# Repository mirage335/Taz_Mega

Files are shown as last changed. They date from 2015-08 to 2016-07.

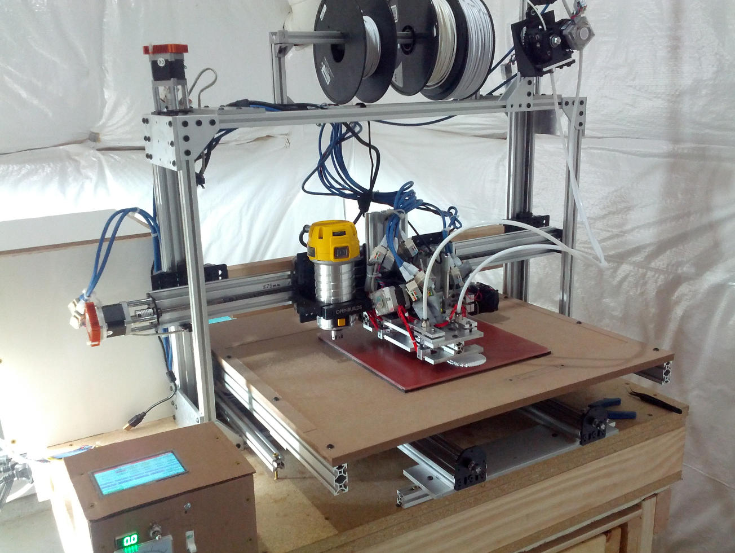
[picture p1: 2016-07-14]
Photos/EarlyPrint.jpg

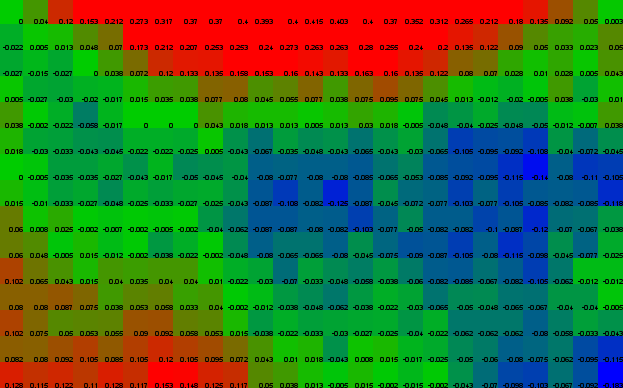
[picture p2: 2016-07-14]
Photos/InitialTopography.jpg

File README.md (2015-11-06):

Copyright (C) 2015 mirage335
See the end of the file for license conditions.
See license.txt for Taz_Mega license conditions.

mirage335.member.hacdc.org

Large-scale advanced multi-tool desktop factory derived from LulzBot Taz. Successor to FlexReplicator.

Intended to simultaneously operate multiple at least milling, laser, extrusion (FDM 3D Printing), and inkjet (powder 3D printing, 2D coloring) tools.

Total cost is estimated at $1,574.45. Normal Taz bulk production costs using this setup would be closer to $1k/unit, probable savings as follows.

Custom Plates - $200/unit.
Y-axis deduplication - $200/unit.
X/Y axis length reduction - $150/unit

#Tweaks
Z-Axis motor mounting plate edges protrude into the frame extrusions, and must be ground slightly to compensate.

Spacer blocks may not leave adequate clearance for the most ideal gantry plate screw locations. Solvable with moderate grinding.

Lock nuts used in wheel assemblies may conflict with some metal plates. Moderate grinding, or use of jam nuts with threadlocker, are solutions.

Y-Axis threaded rod may not be matched to adequately tight tolerances (<<0.3%). Tightly spring-loading all couplings to one of the two threaded rods may alleviate binding at minimal loss of performance. For light-duty work, only one threaded rod is actually necessary.

Do not overtighten joints between gantry plates and aluminum extrusions, as this can significantly overload of the wheel assemblies.

Many more metric screws and Tee Nuts may be required. In particular, some low-profile M5x12mm screws are required to join the Y-axis assembly to the frame. These can be made by grinding down M5x15mm screws from Open Builds.

Right angle brackets from Open Builds may not be suitable for joining the Z-axis extrusions to the frame. Corner cubes are more than adequate.

#Electronics
Duet electronics with PatchRap panel STRONGLY recommended. Heatsinkng the motor drivers would also be wise, as maximum rated current should be used.

#Copyright Extensions
Files embedded into the design by mirage335 with a less restrictive license than GPLv3 place any derrived works under that license. This is definied to include any files pulled into the repository by mirage335 .

#Copyright
This file is part of Taz_Mega.

Taz_Mega is free software: you can redistribute it and/or modify
it under the terms of the GNU General Public License as published by
the Free Software Foundation, either version 3 of the License, or
(at your option) any later version.

Taz_Mega is distributed in the hope that it will be useful,
but WITHOUT ANY WARRANTY; without even the implied warranty of
MERCHANTABILITY or FITNESS FOR A PARTICULAR PURPOSE.  See the
GNU General Public License for more details.

You should have received a copy of the GNU General Public License
along with Taz_Mega.  If not, see <http://www.gnu.org/licenses/>.

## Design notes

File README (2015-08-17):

Copyright (C) 2013 mirage335
See the end of the file for license conditions.
See license.txt for Taz_Mega license conditions.

mirage335.member.hacdc.org

Large-scale advanced multi-tool desktop factory derived from LulzBot Taz. Successor to FlexReplicator.

Intended to simultaneously operate multiple milling, laser, extrusion (FDM 3D Printing), and inkjet (powder 3D printing, 2D coloring) tools.

SolidWorks files will eventually be replaced with FreeCAD, pending initial construction. See render.png for assembly overview, or download free eDrawings viewer for further investigation.

_Copyright Extensions_
Files embedded into the design by mirage335 with a less restrictive license than GPLv3 place any derrived works under that license. This is definied to include any files pulled into the repository by mirage335 .

_Copyright_
This file is part of Taz_Mega.

Taz_Mega is free software: you can redistribute it and/or modify
it under the terms of the GNU General Public License as published by
the Free Software Foundation, either version 3 of the License, or
(at your option) any later version.

Taz_Mega is distributed in the hope that it will be useful,
but WITHOUT ANY WARRANTY; without even the implied warranty of
MERCHANTABILITY or FITNESS FOR A PARTICULAR PURPOSE.  See the
GNU General Public License for more details.

You should have received a copy of the GNU General Public License
along with Taz_Mega.  If not, see <http://www.gnu.org/licenses/>.

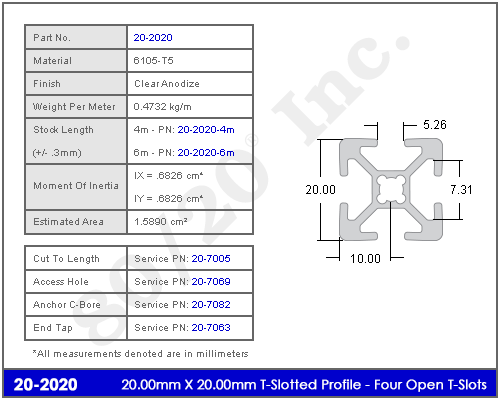
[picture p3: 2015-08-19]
_hardware/Extrusions/_ref/8020profile.gif

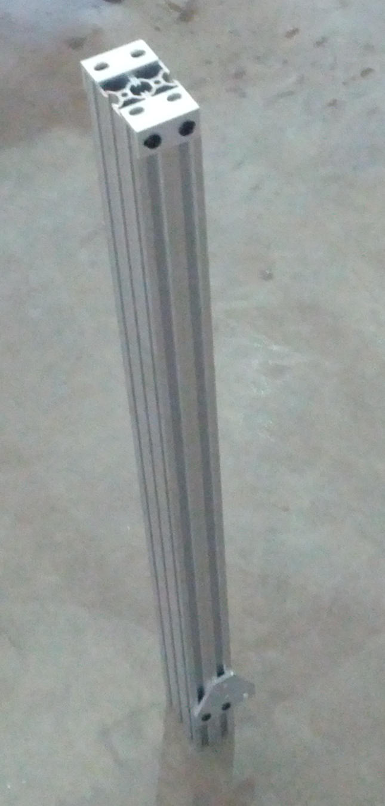
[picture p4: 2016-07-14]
Photos/EqualLength.jpg

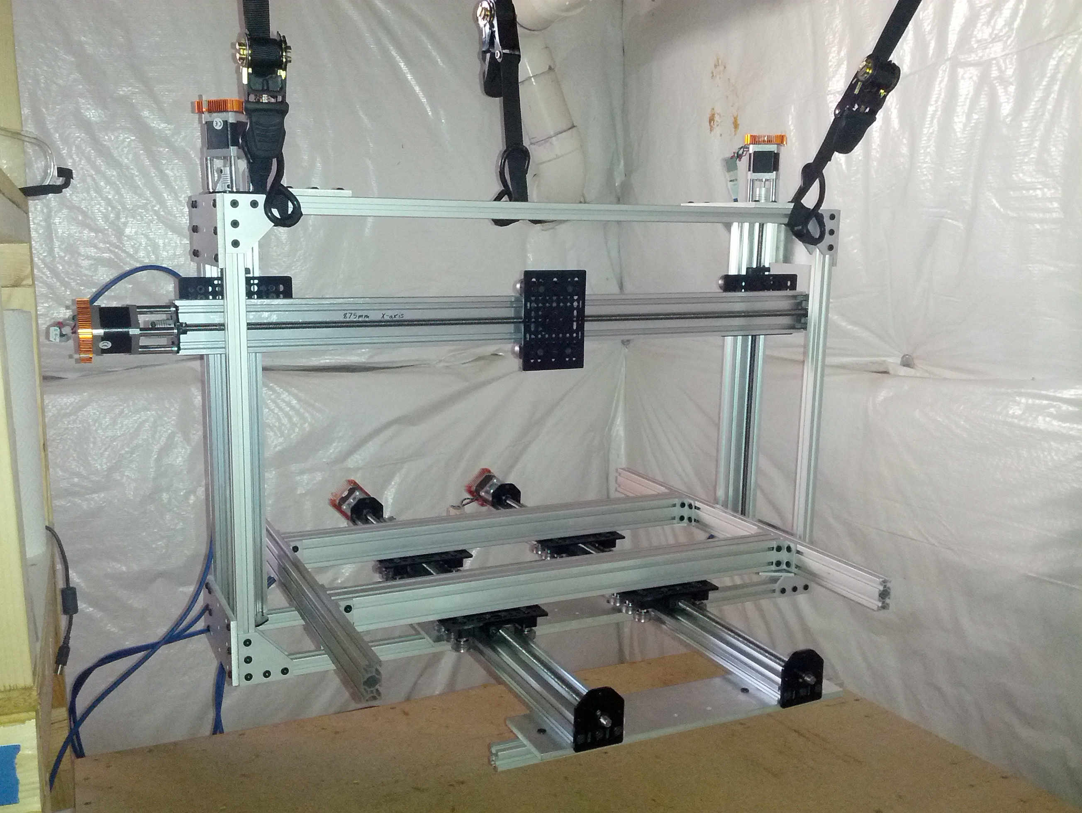
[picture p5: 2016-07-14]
Photos/Suspended.jpg

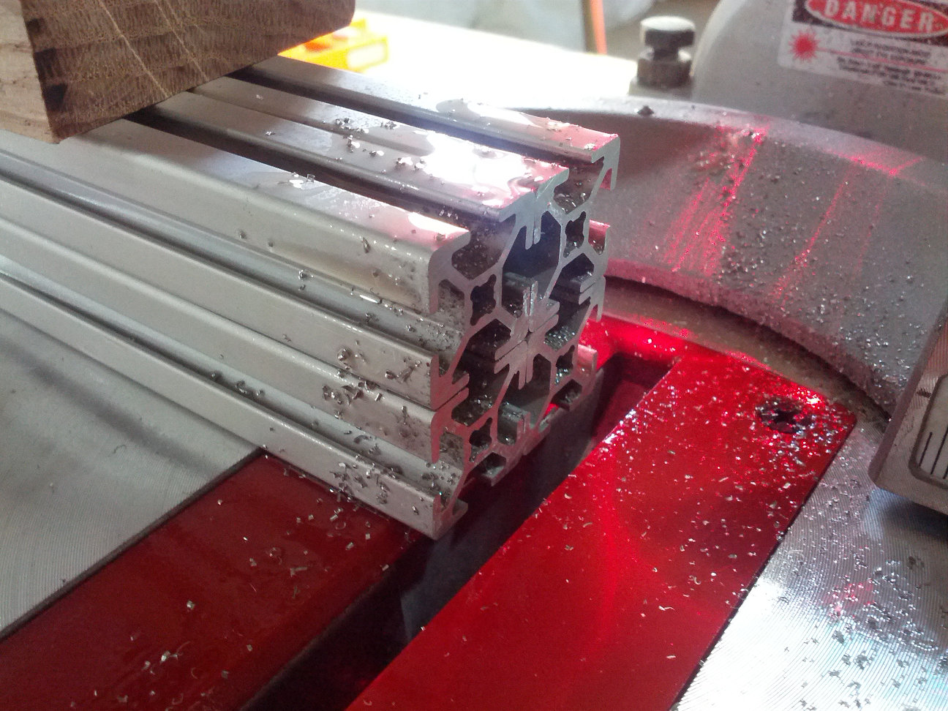
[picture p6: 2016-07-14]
Photos/Cutting.jpg

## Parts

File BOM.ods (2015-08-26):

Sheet: Total_OpenBuilds_DeDup
Description | Qualifiers | Qty | Multiplier | Total | Cost | Total | Supplier
ACME Anti-Backlash Nut Block |  |  |  | 7 | $9.85 | $68.95 | http://openbuildspartstore.com/anti-backlash-nut-block-for-8mm-metric-acme-lead-screw/
ACME LeadScrew |  |  |  | 5 | $31.50 | $157.50 | http://openbuildspartstore.com/8mm-metric-acme-lead-screw/
Cube Corner Connector |  |  |  | 8 | $3.25 | $26.00 | http://openbuildspartstore.com/cube-corner-connector/
Eccentric Spacer, 6mm |  |  |  | 21 | $2.00 | $42.00 | http://openbuildspartstore.com/eccentric-spacer/
Flexible Coupling |  |  |  | 5 | $6.35 | $31.75 | http://openbuildspartstore.com/5mm-8mm-flexible-coupling/
Gantry Plates, Universal V-Slot |  |  |  | 7 | $12.00 | $84.00 | http://openbuildspartstore.com/v-slot-gantry-plates/
Joining Plate, 90deg |  |  |  | 8 | $4.80 | $38.40 | http://openbuildspartstore.com/90-degree-joining-plate/
Joining Plate, T |  |  |  | 4 | $4.65 | $18.60 | http://openbuildspartstore.com/t-joining-plate/
L Bracket | Double |  |  | 6 | $1.50 | $9.00 | http://openbuildspartstore.com/l-bracket/
L Bracket | Tripple |  |  | 6 | $1.50 | $9.00 | http://openbuildspartstore.com/l-bracket/
Lock Collar |  |  |  | 15 | $0.90 | $13.50 | http://openbuildspartstore.com/lock-collar/
Low Profile M5 35mm Screws |  |  |  | 42 | $0.20 | $8.40 | http://openbuildspartstore.com/low-profile-screws-m5/
M3 45mm Screw |  |  |  | 15 | $0.25 | $3.75 | http://openbuildspartstore.com/m3-cap-head-screws/
Screw-M5x10 |  |  |  | 130 | $0.13 | $16.38 | http://openbuildspartstore.com/low-profile-screws-m5/
Screw-M5x8 |  |  |  | 130 | $0.13 | $16.38 | http://openbuildspartstore.com/low-profile-screws-m5/
Set Screw |  |  |  | 15 | $0.07 | $1.05 | http://openbuildspartstore.com/set-screw/
Spacer Blocks |  |  |  | 14 | $3.95 | $55.30 | http://openbuildspartstore.com/spacer-block/
Spacer, 35mm Aluminum |  |  |  | 15 | $0.70 | $10.50 | http://openbuildspartstore.com/aluminum-spacers/
Spacer, 6mm Aluminum |  |  |  | 42 | $0.30 | $12.60 | http://openbuildspartstore.com/aluminum-spacers/
TeeNut-M5x10 |  |  |  | 130 | $0.20 | $25.74 | http://openbuildspartstore.com/tee-nuts-25-pack/
Threaded Rod Motor Mount Plates, NEMA17 |  |  |  | 10 | $6.95 | $69.50 | http://openbuildspartstore.com/threaded-rod-plate-for-nema-17-stepper-motor/
Thruster Bearings |  |  |  | 15 | $1.00 | $15.00 | http://openbuildspartstore.com/ball-bearing-688z-8x16x5/
V-Slot Rail |  |  |  | 3 | $15.50 | $46.50 | http://openbuildspartstore.com/v-slot-linear-rail/
V-Slot Rail | 500mm |  |  | 2 | $7.50 | $15.00 | http://openbuildspartstore.com/v-slot-linear-rail/
Wheel Kits |  |  |  | 42 | $6.75 | $283.50 | http://openbuildspartstore.com/xtreme-solid-v-wheel-kit/
 |  |  |  |  |  | $1,078.30
 |  |  |  |  |  | $1,078.30

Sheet: Total_OpenBuilds
Description | Qualifiers | Qty | Multiplier | Total | Cost | Total | Supplier
Flexible Coupling |  | 1 | 1 | 1 | $6.35 | $6.35 | http://openbuildspartstore.com/5mm-8mm-flexible-coupling/
Flexible Coupling |  | 1 | 2 | 2 | $6.35 | $12.70 | http://openbuildspartstore.com/5mm-8mm-flexible-coupling/
Flexible Coupling |  | 1 | 2 | 2 | $6.35 | $12.70 | http://openbuildspartstore.com/5mm-8mm-flexible-coupling/
ACME LeadScrew |  | 1 | 1 | 1 | $31.50 | $31.50 | http://openbuildspartstore.com/8mm-metric-acme-lead-screw/
ACME LeadScrew |  | 1 | 2 | 2 | $31.50 | $63.00 | http://openbuildspartstore.com/8mm-metric-acme-lead-screw/
ACME LeadScrew |  | 1 | 2 | 2 | $31.50 | $63.00 | http://openbuildspartstore.com/8mm-metric-acme-lead-screw/
Joining Plate, 90deg |  | 8 | 1 | 8 | $4.80 | $38.40 | http://openbuildspartstore.com/90-degree-joining-plate/
Spacer, 35mm Aluminum |  | 3 | 1 | 3 | $0.70 | $2.10 | http://openbuildspartstore.com/aluminum-spacers/
Spacer, 6mm Aluminum |  | 6 | 1 | 6 | $0.30 | $1.80 | http://openbuildspartstore.com/aluminum-spacers/
Spacer, 35mm Aluminum |  | 3 | 2 | 6 | $0.70 | $4.20 | http://openbuildspartstore.com/aluminum-spacers/
Spacer, 6mm Aluminum |  | 6 | 4 | 24 | $0.30 | $7.20 | http://openbuildspartstore.com/aluminum-spacers/
Spacer, 35mm Aluminum |  | 3 | 2 | 6 | $0.70 | $4.20 | http://openbuildspartstore.com/aluminum-spacers/
Spacer, 6mm Aluminum |  | 6 | 2 | 12 | $0.30 | $3.60 | http://openbuildspartstore.com/aluminum-spacers/
ACME Anti-Backlash Nut Block |  | 1 | 1 | 1 | $9.85 | $9.85 | http://openbuildspartstore.com/anti-backlash-nut-block-for-8mm-metric-acme-lead-screw/
ACME Anti-Backlash Nut Block |  | 1 | 4 | 4 | $9.85 | $39.40 | http://openbuildspartstore.com/anti-backlash-nut-block-for-8mm-metric-acme-lead-screw/
ACME Anti-Backlash Nut Block |  | 1 | 2 | 2 | $9.85 | $19.70 | http://openbuildspartstore.com/anti-backlash-nut-block-for-8mm-metric-acme-lead-screw/
Thruster Bearings |  | 3 | 1 | 3 | $1.00 | $3.00 | http://openbuildspartstore.com/ball-bearing-688z-8x16x5/
Thruster Bearings |  | 3 | 2 | 6 | $1.00 | $6.00 | http://openbuildspartstore.com/ball-bearing-688z-8x16x5/
Thruster Bearings |  | 3 | 2 | 6 | $1.00 | $6.00 | http://openbuildspartstore.com/ball-bearing-688z-8x16x5/
Cube Corner Connector |  | 8 | 1 | 8 | $3.25 | $26.00 | http://openbuildspartstore.com/cube-corner-connector/
Eccentric Spacer, 6mm |  | 3 | 1 | 3 | $2.00 | $6.00 | http://openbuildspartstore.com/eccentric-spacer/
Eccentric Spacer, 6mm |  | 3 | 4 | 12 | $2.00 | $24.00 | http://openbuildspartstore.com/eccentric-spacer/
Eccentric Spacer, 6mm |  | 3 | 2 | 6 | $2.00 | $12.00 | http://openbuildspartstore.com/eccentric-spacer/
L Bracket | Double | 6 | 1 | 6 | $1.50 | $9.00 | http://openbuildspartstore.com/l-bracket/
L Bracket | Tripple | 6 | 1 | 6 | $1.50 | $9.00 | http://openbuildspartstore.com/l-bracket/
Lock Collar |  | 3 | 1 | 3 | $0.90 | $2.70 | http://openbuildspartstore.com/lock-collar/
Lock Collar |  | 3 | 2 | 6 | $0.90 | $5.40 | http://openbuildspartstore.com/lock-collar/
Lock Collar |  | 3 | 2 | 6 | $0.90 | $5.40 | http://openbuildspartstore.com/lock-collar/
Screw-M5x8 |  | 130 | 1 | 130 | $0.13 | $16.38 | http://openbuildspartstore.com/low-profile-screws-m5/
Screw-M5x10 |  | 130 | 1 | 130 | $0.13 | $16.38 | http://openbuildspartstore.com/low-profile-screws-m5/
Low Profile M5 35mm Screws |  | 6 | 1 | 6 | $0.20 | $1.20 | http://openbuildspartstore.com/low-profile-screws-m5/
Low Profile M5 35mm Screws |  | 6 | 4 | 24 | $0.20 | $4.80 | http://openbuildspartstore.com/low-profile-screws-m5/
Low Profile M5 35mm Screws |  | 6 | 2 | 12 | $0.20 | $2.40 | http://openbuildspartstore.com/low-profile-screws-m5/
M3 45mm Screw |  | 3 | 1 | 3 | $0.25 | $0.75 | http://openbuildspartstore.com/m3-cap-head-screws/
M3 45mm Screw |  | 3 | 2 | 6 | $0.25 | $1.50 | http://openbuildspartstore.com/m3-cap-head-screws/
M3 45mm Screw |  | 3 | 2 | 6 | $0.25 | $1.50 | http://openbuildspartstore.com/m3-cap-head-screws/
Set Screw |  | 3 | 1 | 3 | $0.07 | $0.21 | http://openbuildspartstore.com/set-screw/
Set Screw |  | 3 | 2 | 6 | $0.07 | $0.42 | http://openbuildspartstore.com/set-screw/
Set Screw |  | 3 | 2 | 6 | $0.07 | $0.42 | http://openbuildspartstore.com/set-screw/
Spacer Blocks |  | 2 | 1 | 2 | $3.95 | $7.90 | http://openbuildspartstore.com/spacer-block/
Spacer Blocks |  | 2 | 4 | 8 | $3.95 | $31.60 | http://openbuildspartstore.com/spacer-block/
Spacer Blocks |  | 2 | 2 | 4 | $3.95 | $15.80 | http://openbuildspartstore.com/spacer-block/
Joining Plate, T |  | 4 | 1 | 4 | $4.65 | $18.60 | http://openbuildspartstore.com/t-joining-plate/
TeeNut-M5x10 |  | 130 | 1 | 130 | $0.20 | $25.74 | http://openbuildspartstore.com/tee-nuts-25-pack/
Threaded Rod Motor Mount Plates, NEMA17 |  | 2 | 1 | 2 | $6.95 | $13.90 | http://openbuildspartstore.com/threaded-rod-plate-for-nema-17-stepper-motor/
Threaded Rod Motor Mount Plates, NEMA17 |  | 2 | 2 | 4 | $6.95 | $27.80 | http://openbuildspartstore.com/threaded-rod-plate-for-nema-17-stepper-motor/
Threaded Rod Motor Mount Plates, NEMA17 |  | 2 | 2 | 4 | $6.95 | $27.80 | http://openbuildspartstore.com/threaded-rod-plate-for-nema-17-stepper-motor/
Gantry Plates, Universal V-Slot |  | 1 | 1 | 1 | $12.00 | $12.00 | http://openbuildspartstore.com/v-slot-gantry-plates/
Gantry Plates, Universal V-Slot |  | 1 | 4 | 4 | $12.00 | $48.00 | http://openbuildspartstore.com/v-slot-gantry-plates/
Gantry Plates, Universal V-Slot |  | 1 | 2 | 2 | $12.00 | $24.00 | http://openbuildspartstore.com/v-slot-gantry-plates/
V-Slot Rail |  | 1 | 1 | 1 | $15.50 | $15.50 | http://openbuildspartstore.com/v-slot-linear-rail/
V-Slot Rail |  | 1 | 2 | 2 | $15.50 | $31.00 | http://openbuildspartstore.com/v-slot-linear-rail/
V-Slot Rail | 500mm | 1 | 2 | 2 | $7.50 | $15.00 | http://openbuildspartstore.com/v-slot-linear-rail/
Wheel Kits |  | 6 | 1 | 6 | $6.75 | $40.50 | http://openbuildspartstore.com/xtreme-solid-v-wheel-kit/
Wheel Kits |  | 6 | 4 | 24 | $6.75 | $162.00 | http://openbuildspartstore.com/xtreme-solid-v-wheel-kit/
Wheel Kits |  | 6 | 2 | 12 | $6.75 | $81.00 | http://openbuildspartstore.com/xtreme-solid-v-wheel-kit/
 |  |  |  |  |  | $1,078.30

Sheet: Total_SupplierSorted
Description | Qualifiers | Qty | Multiplier | Total | Cost | Total | Supplier
Flexible Coupling |  | 1 | 1 | 1 | $6.35 | $6.35 | http://openbuildspartstore.com/5mm-8mm-flexible-coupling/
Flexible Coupling |  | 1 | 2 | 2 | $6.35 | $12.70 | http://openbuildspartstore.com/5mm-8mm-flexible-coupling/
Flexible Coupling |  | 1 | 2 | 2 | $6.35 | $12.70 | http://openbuildspartstore.com/5mm-8mm-flexible-coupling/
ACME LeadScrew |  | 1 | 1 | 1 | $31.50 | $31.50 | http://openbuildspartstore.com/8mm-metric-acme-lead-screw/
ACME LeadScrew |  | 1 | 2 | 2 | $31.50 | $63.00 | http://openbuildspartstore.com/8mm-metric-acme-lead-screw/
ACME LeadScrew |  | 1 | 2 | 2 | $31.50 | $63.00 | http://openbuildspartstore.com/8mm-metric-acme-lead-screw/
Joining Plate, 90deg |  | 8 | 1 | 8 | $4.80 | $38.40 | http://openbuildspartstore.com/90-degree-joining-plate/
Spacer, 35mm Aluminum |  | 3 | 1 | 3 | $0.70 | $2.10 | http://openbuildspartstore.com/aluminum-spacers/
Spacer, 6mm Aluminum |  | 6 | 1 | 6 | $0.30 | $1.80 | http://openbuildspartstore.com/aluminum-spacers/
Spacer, 35mm Aluminum |  | 3 | 2 | 6 | $0.70 | $4.20 | http://openbuildspartstore.com/aluminum-spacers/
Spacer, 6mm Aluminum |  | 6 | 4 | 24 | $0.30 | $7.20 | http://openbuildspartstore.com/aluminum-spacers/
Spacer, 35mm Aluminum |  | 3 | 2 | 6 | $0.70 | $4.20 | http://openbuildspartstore.com/aluminum-spacers/
Spacer, 6mm Aluminum |  | 6 | 2 | 12 | $0.30 | $3.60 | http://openbuildspartstore.com/aluminum-spacers/
ACME Anti-Backlash Nut Block |  | 1 | 1 | 1 | $9.85 | $9.85 | http://openbuildspartstore.com/anti-backlash-nut-block-for-8mm-metric-acme-lead-screw/
ACME Anti-Backlash Nut Block |  | 1 | 4 | 4 | $9.85 | $39.40 | http://openbuildspartstore.com/anti-backlash-nut-block-for-8mm-metric-acme-lead-screw/
ACME Anti-Backlash Nut Block |  | 1 | 2 | 2 | $9.85 | $19.70 | http://openbuildspartstore.com/anti-backlash-nut-block-for-8mm-metric-acme-lead-screw/
Thruster Bearings |  | 3 | 1 | 3 | $1.00 | $3.00 | http://openbuildspartstore.com/ball-bearing-688z-8x16x5/
Thruster Bearings |  | 3 | 2 | 6 | $1.00 | $6.00 | http://openbuildspartstore.com/ball-bearing-688z-8x16x5/
Thruster Bearings |  | 3 | 2 | 6 | $1.00 | $6.00 | http://openbuildspartstore.com/ball-bearing-688z-8x16x5/
Cube Corner Connector |  | 8 | 1 | 8 | $3.25 | $26.00 | http://openbuildspartstore.com/cube-corner-connector/
Eccentric Spacer, 6mm |  | 3 | 1 | 3 | $2.00 | $6.00 | http://openbuildspartstore.com/eccentric-spacer/
Eccentric Spacer, 6mm |  | 3 | 4 | 12 | $2.00 | $24.00 | http://openbuildspartstore.com/eccentric-spacer/
Eccentric Spacer, 6mm |  | 3 | 2 | 6 | $2.00 | $12.00 | http://openbuildspartstore.com/eccentric-spacer/
L Bracket | Double | 6 | 1 | 6 | $1.50 | $9.00 | http://openbuildspartstore.com/l-bracket/
L Bracket | Tripple | 6 | 1 | 6 | $1.50 | $9.00 | http://openbuildspartstore.com/l-bracket/
Lock Collar |  | 3 | 1 | 3 | $0.90 | $2.70 | http://openbuildspartstore.com/lock-collar/
Lock Collar |  | 3 | 2 | 6 | $0.90 | $5.40 | http://openbuildspartstore.com/lock-collar/
Lock Collar |  | 3 | 2 | 6 | $0.90 | $5.40 | http://openbuildspartstore.com/lock-collar/
Screw-M5x8 |  | 130 | 1 | 130 | $0.13 | $16.38 | http://openbuildspartstore.com/low-profile-screws-m5/
Screw-M5x10 |  | 130 | 1 | 130 | $0.13 | $16.38 | http://openbuildspartstore.com/low-profile-screws-m5/
Low Profile M5 35mm Screws |  | 6 | 1 | 6 | $0.20 | $1.20 | http://openbuildspartstore.com/low-profile-screws-m5/
Low Profile M5 35mm Screws |  | 6 | 4 | 24 | $0.20 | $4.80 | http://openbuildspartstore.com/low-profile-screws-m5/
Low Profile M5 35mm Screws |  | 6 | 2 | 12 | $0.20 | $2.40 | http://openbuildspartstore.com/low-profile-screws-m5/
M3 45mm Screw |  | 3 | 1 | 3 | $0.25 | $0.75 | http://openbuildspartstore.com/m3-cap-head-screws/
M3 45mm Screw |  | 3 | 2 | 6 | $0.25 | $1.50 | http://openbuildspartstore.com/m3-cap-head-screws/
M3 45mm Screw |  | 3 | 2 | 6 | $0.25 | $1.50 | http://openbuildspartstore.com/m3-cap-head-screws/
Set Screw |  | 3 | 1 | 3 | $0.07 | $0.21 | http://openbuildspartstore.com/set-screw/
Set Screw |  | 3 | 2 | 6 | $0.07 | $0.42 | http://openbuildspartstore.com/set-screw/
Set Screw |  | 3 | 2 | 6 | $0.07 | $0.42 | http://openbuildspartstore.com/set-screw/
Spacer Blocks |  | 2 | 1 | 2 | $3.95 | $7.90 | http://openbuildspartstore.com/spacer-block/
Spacer Blocks |  | 2 | 4 | 8 | $3.95 | $31.60 | http://openbuildspartstore.com/spacer-block/
Spacer Blocks |  | 2 | 2 | 4 | $3.95 | $15.80 | http://openbuildspartstore.com/spacer-block/
Joining Plate, T |  | 4 | 1 | 4 | $4.65 | $18.60 | http://openbuildspartstore.com/t-joining-plate/
TeeNut-M5x10 |  | 130 | 1 | 130 | $0.20 | $25.74 | http://openbuildspartstore.com/tee-nuts-25-pack/
Threaded Rod Motor Mount Plates, NEMA17 |  | 2 | 1 | 2 | $6.95 | $13.90 | http://openbuildspartstore.com/threaded-rod-plate-for-nema-17-stepper-motor/
Threaded Rod Motor Mount Plates, NEMA17 |  | 2 | 2 | 4 | $6.95 | $27.80 | http://openbuildspartstore.com/threaded-rod-plate-for-nema-17-stepper-motor/
Threaded Rod Motor Mount Plates, NEMA17 |  | 2 | 2 | 4 | $6.95 | $27.80 | http://openbuildspartstore.com/threaded-rod-plate-for-nema-17-stepper-motor/
Gantry Plates, Universal V-Slot |  | 1 | 1 | 1 | $12.00 | $12.00 | http://openbuildspartstore.com/v-slot-gantry-plates/
Gantry Plates, Universal V-Slot |  | 1 | 4 | 4 | $12.00 | $48.00 | http://openbuildspartstore.com/v-slot-gantry-plates/
Gantry Plates, Universal V-Slot |  | 1 | 2 | 2 | $12.00 | $24.00 | http://openbuildspartstore.com/v-slot-gantry-plates/
V-Slot Rail |  | 1 | 1 | 1 | $15.50 | $15.50 | http://openbuildspartstore.com/v-slot-linear-rail/
V-Slot Rail |  | 1 | 2 | 2 | $15.50 | $31.00 | http://openbuildspartstore.com/v-slot-linear-rail/
V-Slot Rail | 500mm | 1 | 2 | 2 | $7.50 | $15.00 | http://openbuildspartstore.com/v-slot-linear-rail/
Wheel Kits |  | 6 | 1 | 6 | $6.75 | $40.50 | http://openbuildspartstore.com/xtreme-solid-v-wheel-kit/
Wheel Kits |  | 6 | 4 | 24 | $6.75 | $162.00 | http://openbuildspartstore.com/xtreme-solid-v-wheel-kit/
Wheel Kits |  | 6 | 2 | 12 | $6.75 | $81.00 | http://openbuildspartstore.com/xtreme-solid-v-wheel-kit/
Extrusion, 20-2020 | 610mm | 4 | 1 | 4 | $5.79 | $23.16 | http://www.amazon.com/80-20-20-2020-T-SLOTTED-EXTRUSION/dp/B001F0I3F8
Extrusion, 20-2020 | 1210mm | 4 | 1 | 4 | $9.64 | $38.56 | http://www.amazon.com/80-20-20-2020-T-SLOTTED-EXTRUSION/dp/B001F0K4NW
Extrusion, 20-2040 |  | 2 | 1 | 2 | $8.66 | $17.32 | http://www.amazon.com/80-20-20-2040-T-SLOTTED-EXTRUSION/dp/B001F0G6CU
Extrusion, 20-4040 |  | 1 | 1 | 1 | $13.54 | $13.54 | http://www.amazon.com/80-20-20-4040-T-Slotted-Extrusion/dp/B001F0F1BC
XY_Plate | CUSTOM | 1 | 1 | 1 |  | $90.81 | http://www.emachineshop.com/
XY_EndPlate | CUSTOM | 2 | 1 | 2 |  | $104.27 | http://www.emachineshop.com/
GantryPlate | CUSTOM | 6 | 1 | 6 | $25.00 | $136.72 | http://www.emachineshop.com/
M5 Jam Nuts |  | 6 | 1 | 6 | $0.05 | $0.29 | https://www.fastenal.com/products/details/MJ2540000A20000?r=~|categoryl1:%22600000%20Fasteners%22|~%20~|categoryl2:%22600072%20Nuts%22|~%20~|categoryl3:%22600080%20Jam%20Nuts%22|~%20~|sattr01:^Metric$|~%20~|sattr04:^M5-0.8$|~
M5 Jam Nuts |  | 6 | 4 | 24 | $0.05 | $1.16 | https://www.fastenal.com/products/details/MJ2540000A20000?r=~|categoryl1:%22600000%20Fasteners%22|~%20~|categoryl2:%22600072%20Nuts%22|~%20~|categoryl3:%22600080%20Jam%20Nuts%22|~%20~|sattr01:^Metric$|~%20~|sattr04:^M5-0.8$|~
M5 Jam Nuts |  | 6 | 2 | 12 | $0.05 | $0.58 | https://www.fastenal.com/products/details/MJ2540000A20000?r=~|categoryl1:%22600000%20Fasteners%22|~%20~|categoryl2:%22600072%20Nuts%22|~%20~|categoryl3:%22600080%20Jam%20Nuts%22|~%20~|sattr01:^Metric$|~%20~|sattr04:^M5-0.8$|~
NEMA17 Motor |  | 1 | 1 | 1 | $13.95 | $13.95 | https://www.lulzbot.com/products/nema-17-stepper-motor
NEMA17 Motor |  | 1 | 2 | 2 | $13.95 | $27.90 | https://www.lulzbot.com/products/nema-17-stepper-motor
NEMA17 Motor |  | 1 | 2 | 2 | $13.95 | $27.90 | https://www.lulzbot.com/products/nema-17-stepper-motor
 |  |  |  |  |  | $1,574.45

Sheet: Total
Description | Qualifiers | Qty | Multiplier | Total | Cost | Total | Supplier
L Bracket | Double | 6 | 1 | 6 | $1.50 | $9.00 | http://openbuildspartstore.com/l-bracket/
Joining Plate, T |  | 4 | 1 | 4 | $4.65 | $18.60 | http://openbuildspartstore.com/t-joining-plate/
Extrusion, 20-2040 |  | 2 | 1 | 2 | $8.66 | $17.32 | http://www.amazon.com/80-20-20-2040-T-SLOTTED-EXTRUSION/dp/B001F0G6CU
Extrusion, 20-4040 |  | 1 | 1 | 1 | $13.54 | $13.54 | http://www.amazon.com/80-20-20-4040-T-Slotted-Extrusion/dp/B001F0F1BC
XY_Plate | CUSTOM | 1 | 1 | 1 |  | $90.81 | http://www.emachineshop.com/
XY_EndPlate | CUSTOM | 2 | 1 | 2 |  | $104.27 | http://www.emachineshop.com/
Joining Plate, 90deg |  | 8 | 1 | 8 | $4.80 | $38.40 | http://openbuildspartstore.com/90-degree-joining-plate/
Cube Corner Connector |  | 8 | 1 | 8 | $3.25 | $26.00 | http://openbuildspartstore.com/cube-corner-connector/
L Bracket | Tripple | 6 | 1 | 6 | $1.50 | $9.00 | http://openbuildspartstore.com/l-bracket/
Extrusion, 20-2020 | 1210mm | 4 | 1 | 4 | $9.64 | $38.56 | http://www.amazon.com/80-20-20-2020-T-SLOTTED-EXTRUSION/dp/B001F0K4NW
Extrusion, 20-2020 | 610mm | 4 | 1 | 4 | $5.79 | $23.16 | http://www.amazon.com/80-20-20-2020-T-SLOTTED-EXTRUSION/dp/B001F0I3F8
GantryPlate | CUSTOM | 6 | 1 | 6 | $25.00 | $136.72 | http://www.emachineshop.com/
Screw-M5x8 |  | 130 | 1 | 130 | $0.13 | $16.38 | http://openbuildspartstore.com/low-profile-screws-m5/
Screw-M5x10 |  | 130 | 1 | 130 | $0.13 | $16.38 | http://openbuildspartstore.com/low-profile-screws-m5/
TeeNut-M5x10 |  | 130 | 1 | 130 | $0.20 | $25.74 | http://openbuildspartstore.com/tee-nuts-25-pack/
ACME LeadScrew |  | 1 | 1 | 1 | $31.50 | $31.50 | http://openbuildspartstore.com/8mm-metric-acme-lead-screw/
V-Slot Rail |  | 1 | 1 | 1 | $15.50 | $15.50 | http://openbuildspartstore.com/v-slot-linear-rail/
 |  |  | 1 | 0
Threaded Rod Motor Mount Plates, NEMA17 |  | 2 | 1 | 2 | $6.95 | $13.90 | http://openbuildspartstore.com/threaded-rod-plate-for-nema-17-stepper-motor/
M3 45mm Screw |  | 3 | 1 | 3 | $0.25 | $0.75 | http://openbuildspartstore.com/m3-cap-head-screws/
Spacer, 35mm Aluminum |  | 3 | 1 | 3 | $0.70 | $2.10 | http://openbuildspartstore.com/aluminum-spacers/
Set Screw |  | 3 | 1 | 3 | $0.07 | $0.21 | http://openbuildspartstore.com/set-screw/
Lock Collar |  | 3 | 1 | 3 | $0.90 | $2.70 | http://openbuildspartstore.com/lock-collar/
Thruster Bearings |  | 3 | 1 | 3 | $1.00 | $3.00 | http://openbuildspartstore.com/ball-bearing-688z-8x16x5/
Flexible Coupling |  | 1 | 1 | 1 | $6.35 | $6.35 | http://openbuildspartstore.com/5mm-8mm-flexible-coupling/
 |  |  | 1 | 0
NEMA17 Motor |  | 1 | 1 | 1 | $13.95 | $13.95 | https://www.lulzbot.com/products/nema-17-stepper-motor
 |  |  | 1 | 0
Spacer Blocks |  | 2 | 1 | 2 | $3.95 | $7.90 | http://openbuildspartstore.com/spacer-block/
Gantry Plates, Universal V-Slot |  | 1 | 1 | 1 | $12.00 | $12.00 | http://openbuildspartstore.com/v-slot-gantry-plates/
ACME Anti-Backlash Nut Block |  | 1 | 1 | 1 | $9.85 | $9.85 | http://openbuildspartstore.com/anti-backlash-nut-block-for-8mm-metric-acme-lead-screw/
 |  |  | 1 | 0
Wheel Kits |  | 6 | 1 | 6 | $6.75 | $40.50 | http://openbuildspartstore.com/xtreme-solid-v-wheel-kit/
M5 Jam Nuts |  | 6 | 1 | 6 | $0.05 | $0.29 | https://www.fastenal.com/products/details/MJ2540000A20000?r=~|categoryl1:%22600000%20Fasteners%22|~%20~|categoryl2:%22600072%20Nuts%22|~%20~|categoryl3:%22600080%20Jam%20Nuts%22|~%20~|sattr01:^Metric$|~%20~|sattr04:^M5-0.8$|~
Low Profile M5 35mm Screws |  | 6 | 1 | 6 | $0.20 | $1.20 | http://openbuildspartstore.com/low-profile-screws-m5/
Spacer, 6mm Aluminum |  | 6 | 1 | 6 | $0.30 | $1.80 | http://openbuildspartstore.com/aluminum-spacers/
Eccentric Spacer, 6mm |  | 3 | 1 | 3 | $2.00 | $6.00 | http://openbuildspartstore.com/eccentric-spacer/
ACME LeadScrew |  | 1 | 2 | 2 | $31.50 | $63.00 | http://openbuildspartstore.com/8mm-metric-acme-lead-screw/
V-Slot Rail |  | 1 | 2 | 2 | $15.50 | $31.00 | http://openbuildspartstore.com/v-slot-linear-rail/
 |  |  | 2 | 0
Threaded Rod Motor Mount Plates, NEMA17 |  | 2 | 2 | 4 | $6.95 | $27.80 | http://openbuildspartstore.com/threaded-rod-plate-for-nema-17-stepper-motor/
M3 45mm Screw |  | 3 | 2 | 6 | $0.25 | $1.50 | http://openbuildspartstore.com/m3-cap-head-screws/
Spacer, 35mm Aluminum |  | 3 | 2 | 6 | $0.70 | $4.20 | http://openbuildspartstore.com/aluminum-spacers/
Lock Collar |  | 3 | 2 | 6 | $0.90 | $5.40 | http://openbuildspartstore.com/lock-collar/
Set Screw |  | 3 | 2 | 6 | $0.07 | $0.42 | http://openbuildspartstore.com/set-screw/
Thruster Bearings |  | 3 | 2 | 6 | $1.00 | $6.00 | http://openbuildspartstore.com/ball-bearing-688z-8x16x5/
Flexible Coupling |  | 1 | 2 | 2 | $6.35 | $12.70 | http://openbuildspartstore.com/5mm-8mm-flexible-coupling/
 |  |  | 2 | 0
NEMA17 Motor |  | 1 | 2 | 2 | $13.95 | $27.90 | https://www.lulzbot.com/products/nema-17-stepper-motor
 |  |  | 2 | 0
Spacer Blocks |  | 2 | 4 | 8 | $3.95 | $31.60 | http://openbuildspartstore.com/spacer-block/
Gantry Plates, Universal V-Slot |  | 1 | 4 | 4 | $12.00 | $48.00 | http://openbuildspartstore.com/v-slot-gantry-plates/
ACME Anti-Backlash Nut Block |  | 1 | 4 | 4 | $9.85 | $39.40 | http://openbuildspartstore.com/anti-backlash-nut-block-for-8mm-metric-acme-lead-screw/
 |  |  | 2 | 0
Wheel Kits |  | 6 | 4 | 24 | $6.75 | $162.00 | http://openbuildspartstore.com/xtreme-solid-v-wheel-kit/
M5 Jam Nuts |  | 6 | 4 | 24 | $0.05 | $1.16 | https://www.fastenal.com/products/details/MJ2540000A20000?r=~|categoryl1:%22600000%20Fasteners%22|~%20~|categoryl2:%22600072%20Nuts%22|~%20~|categoryl3:%22600080%20Jam%20Nuts%22|~%20~|sattr01:^Metric$|~%20~|sattr04:^M5-0.8$|~
Low Profile M5 35mm Screws |  | 6 | 4 | 24 | $0.20 | $4.80 | http://openbuildspartstore.com/low-profile-screws-m5/
Spacer, 6mm Aluminum |  | 6 | 4 | 24 | $0.30 | $7.20 | http://openbuildspartstore.com/aluminum-spacers/
Eccentric Spacer, 6mm |  | 3 | 4 | 12 | $2.00 | $24.00 | http://openbuildspartstore.com/eccentric-spacer/
ACME LeadScrew |  | 1 | 2 | 2 | $31.50 | $63.00 | http://openbuildspartstore.com/8mm-metric-acme-lead-screw/
V-Slot Rail | 500mm | 1 | 2 | 2 | $7.50 | $15.00 | http://openbuildspartstore.com/v-slot-linear-rail/
 |  |  | 2 | 0
Threaded Rod Motor Mount Plates, NEMA17 |  | 2 | 2 | 4 | $6.95 | $27.80 | http://openbuildspartstore.com/threaded-rod-plate-for-nema-17-stepper-motor/
M3 45mm Screw |  | 3 | 2 | 6 | $0.25 | $1.50 | http://openbuildspartstore.com/m3-cap-head-screws/
Spacer, 35mm Aluminum |  | 3 | 2 | 6 | $0.70 | $4.20 | http://openbuildspartstore.com/aluminum-spacers/
Lock Collar |  | 3 | 2 | 6 | $0.90 | $5.40 | http://openbuildspartstore.com/lock-collar/
Set Screw |  | 3 | 2 | 6 | $0.07 | $0.42 | http://openbuildspartstore.com/set-screw/
Thruster Bearings |  | 3 | 2 | 6 | $1.00 | $6.00 | http://openbuildspartstore.com/ball-bearing-688z-8x16x5/
Flexible Coupling |  | 1 | 2 | 2 | $6.35 | $12.70 | http://openbuildspartstore.com/5mm-8mm-flexible-coupling/
 |  |  | 2 | 0
NEMA17 Motor |  | 1 | 2 | 2 | $13.95 | $27.90 | https://www.lulzbot.com/products/nema-17-stepper-motor
 |  |  | 2 | 0
Spacer Blocks |  | 2 | 2 | 4 | $3.95 | $15.80 | http://openbuildspartstore.com/spacer-block/
Gantry Plates, Universal V-Slot |  | 1 | 2 | 2 | $12.00 | $24.00 | http://openbuildspartstore.com/v-slot-gantry-plates/
ACME Anti-Backlash Nut Block |  | 1 | 2 | 2 | $9.85 | $19.70 | http://openbuildspartstore.com/anti-backlash-nut-block-for-8mm-metric-acme-lead-screw/
 |  |  | 2 | 0
Wheel Kits |  | 6 | 2 | 12 | $6.75 | $81.00 | http://openbuildspartstore.com/xtreme-solid-v-wheel-kit/
M5 Jam Nuts |  | 6 | 2 | 12 | $0.05 | $0.58 | https://www.fastenal.com/products/details/MJ2540000A20000?r=~|categoryl1:%22600000%20Fasteners%22|~%20~|categoryl2:%22600072%20Nuts%22|~%20~|categoryl3:%22600080%20Jam%20Nuts%22|~%20~|sattr01:^Metric$|~%20~|sattr04:^M5-0.8$|~
Low Profile M5 35mm Screws |  | 6 | 2 | 12 | $0.20 | $2.40 | http://openbuildspartstore.com/low-profile-screws-m5/
Spacer, 6mm Aluminum |  | 6 | 2 | 12 | $0.30 | $3.60 | http://openbuildspartstore.com/aluminum-spacers/
Eccentric Spacer, 6mm |  | 3 | 2 | 6 | $2.00 | $12.00 | http://openbuildspartstore.com/eccentric-spacer/
 |  |  |  |  |  | $1,574.45

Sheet: Bed
Description | Qualifiers | Qty | Multiplier | Total | Cost | Total | Supplier
L Bracket | Double | 6 | 1 | 6 | $1.50 | $9.00 | http://openbuildspartstore.com/l-bracket/
Joining Plate, T |  | 4 | 1 | 4 | $4.65 | $18.60 | http://openbuildspartstore.com/t-joining-plate/
Extrusion, 20-2040 |  | 2 | 1 | 2 | $8.66 | $17.32 | http://www.amazon.com/80-20-20-2040-T-SLOTTED-EXTRUSION/dp/B001F0G6CU
Extrusion, 20-4040 |  | 1 | 1 | 1 | $13.54 | $13.54 | http://www.amazon.com/80-20-20-4040-T-Slotted-Extrusion/dp/B001F0F1BC
XY_Plate | CUSTOM | 1 | 1 | 1 |  | $90.81 | http://www.emachineshop.com/
XY_EndPlate | CUSTOM | 2 | 1 | 2 |  | $104.27 | http://www.emachineshop.com/

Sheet: Frame
Description | Qualifiers | Qty | Multiplier | Total | Cost | Total | Supplier
Joining Plate, 90deg |  | 8 | 1 | 8 | $4.80 | $38.40 | http://openbuildspartstore.com/90-degree-joining-plate/
Cube Corner Connector |  | 8 | 1 | 8 | $3.25 | $26.00 | http://openbuildspartstore.com/cube-corner-connector/
L Bracket | Tripple | 6 | 1 | 6 | $1.50 | $9.00 | http://openbuildspartstore.com/l-bracket/
Extrusion, 20-2020 | 1210mm | 4 | 1 | 4 | $9.64 | $38.56 | http://www.amazon.com/80-20-20-2020-T-SLOTTED-EXTRUSION/dp/B001F0K4NW
Extrusion, 20-2020 | 610mm | 4 | 1 | 4 | $5.79 | $23.16 | http://www.amazon.com/80-20-20-2020-T-SLOTTED-EXTRUSION/dp/B001F0I3F8
GantryPlate | CUSTOM | 6 | 1 | 6 | $25.00 | $136.72 | http://www.emachineshop.com/
Screw-M5x8 |  | 130 | 1 | 130 | $0.13 | $16.38 | http://openbuildspartstore.com/low-profile-screws-m5/
Screw-M5x10 |  | 130 | 1 | 130 | $0.13 | $16.38 | http://openbuildspartstore.com/low-profile-screws-m5/
TeeNut-M5x10 |  | 130 | 1 | 130 | $0.20 | $25.74 | http://openbuildspartstore.com/tee-nuts-25-pack/

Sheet: X
Description | Qualifiers | Qty | Multiplier | Total | Cost | Total | Supplier
ACME LeadScrew |  | 1 | 1 | 1 | $31.50 | $31.50 | http://openbuildspartstore.com/8mm-metric-acme-lead-screw/
V-Slot Rail |  | 1 | 1 | 1 | $15.50 | $15.50 | http://openbuildspartstore.com/v-slot-linear-rail/
 |  |  | 1 | 0
Threaded Rod Motor Mount Plates, NEMA17 |  | 2 | 1 | 2 | $6.95 | $13.90 | http://openbuildspartstore.com/threaded-rod-plate-for-nema-17-stepper-motor/
M3 45mm Screw |  | 3 | 1 | 3 | $0.25 | $0.75 | http://openbuildspartstore.com/m3-cap-head-screws/
Spacer, 35mm Aluminum |  | 3 | 1 | 3 | $0.70 | $2.10 | http://openbuildspartstore.com/aluminum-spacers/
Set Screw |  | 3 | 1 | 3 | $0.07 | $0.21 | http://openbuildspartstore.com/set-screw/
Lock Collar |  | 3 | 1 | 3 | $0.90 | $2.70 | http://openbuildspartstore.com/lock-collar/
Thruster Bearings |  | 3 | 1 | 3 | $1.00 | $3.00 | http://openbuildspartstore.com/ball-bearing-688z-8x16x5/
Flexible Coupling |  | 1 | 1 | 1 | $6.35 | $6.35 | http://openbuildspartstore.com/5mm-8mm-flexible-coupling/
 |  |  | 1 | 0
NEMA17 Motor |  | 1 | 1 | 1 | $13.95 | $13.95 | https://www.lulzbot.com/products/nema-17-stepper-motor
 |  |  | 1 | 0
Spacer Blocks |  | 2 | 1 | 2 | $3.95 | $7.90 | http://openbuildspartstore.com/spacer-block/
Gantry Plates, Universal V-Slot |  | 1 | 1 | 1 | $12.00 | $12.00 | http://openbuildspartstore.com/v-slot-gantry-plates/
ACME Anti-Backlash Nut Block |  | 1 | 1 | 1 | $9.85 | $9.85 | http://openbuildspartstore.com/anti-backlash-nut-block-for-8mm-metric-acme-lead-screw/
 |  |  | 1 | 0
Wheel Kits |  | 6 | 1 | 6 | $6.75 | $40.50 | http://openbuildspartstore.com/xtreme-solid-v-wheel-kit/
M5 Jam Nuts |  | 6 | 1 | 6 | $0.05 | $0.29 | https://www.fastenal.com/products/details/MJ2540000A20000?r=~|categoryl1:%22600000%20Fasteners%22|~%20~|categoryl2:%22600072%20Nuts%22|~%20~|categoryl3:%22600080%20Jam%20Nuts%22|~%20~|sattr01:^Metric$|~%20~|sattr04:^M5-0.8$|~
Low Profile M5 35mm Screws |  | 6 | 1 | 6 | $0.20 | $1.20 | http://openbuildspartstore.com/low-profile-screws-m5/
Spacer, 6mm Aluminum |  | 6 | 1 | 6 | $0.30 | $1.80 | http://openbuildspartstore.com/aluminum-spacers/
Eccentric Spacer, 6mm |  | 3 | 1 | 3 | $2.00 | $6.00 | http://openbuildspartstore.com/eccentric-spacer/
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

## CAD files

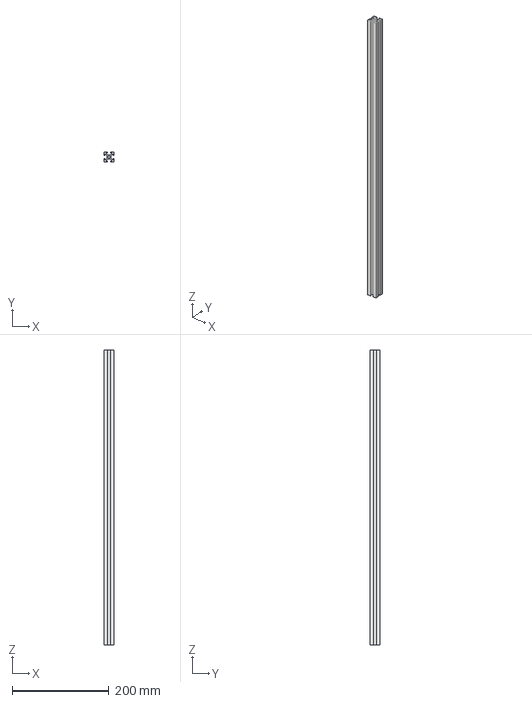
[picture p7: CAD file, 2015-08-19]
_hardware/Extrusions/20series-1x1_610mm.fcstd
20.0 x 20.0 x 610.0 mm

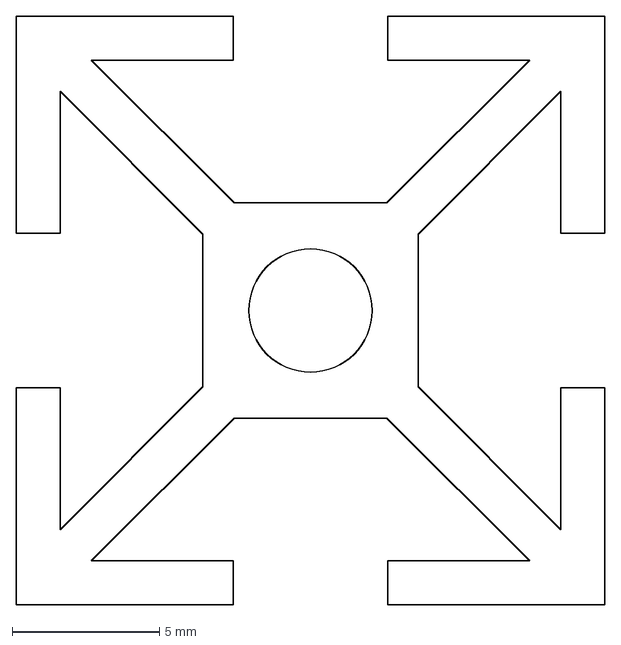
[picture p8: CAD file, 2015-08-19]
_hardware/Extrusions/_ref/20_series.DXF
20.0 x 20.0 mm

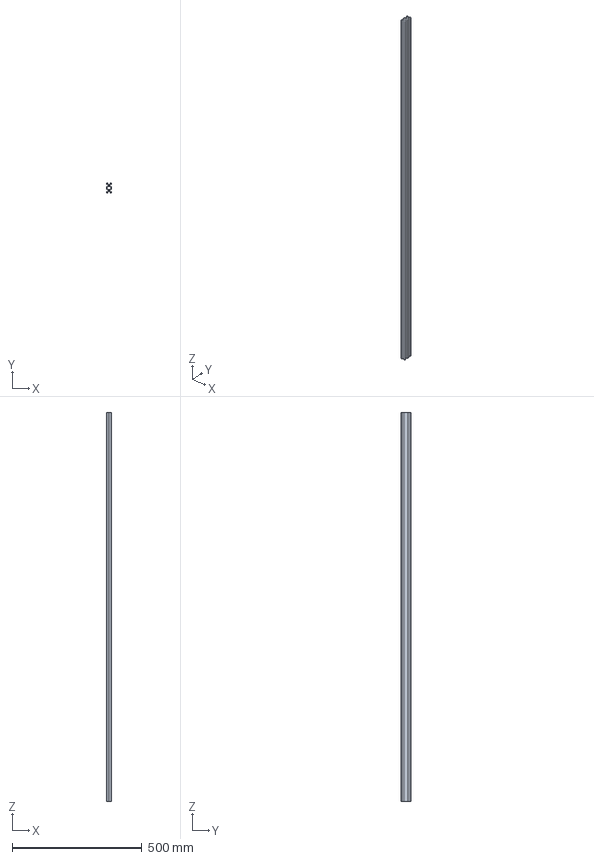
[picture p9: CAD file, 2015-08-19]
_hardware/OpenBuilds/1 - Linear Rail/V-Slot 20x40x1500 Linear Rail.step.fcstd
20.0 x 40.0 x 1500.0 mm

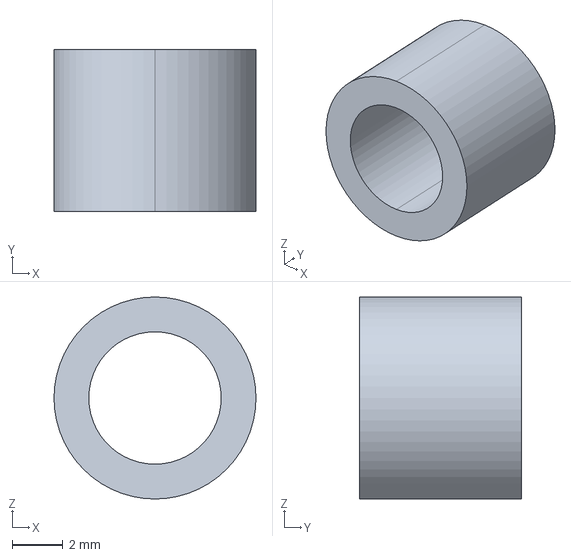
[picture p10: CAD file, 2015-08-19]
_hardware/OpenBuilds/10 - Shims and Spacers/Nylon Spacer 0.25in.step.fcstd
7.94 x 6.35 x 7.94 mm

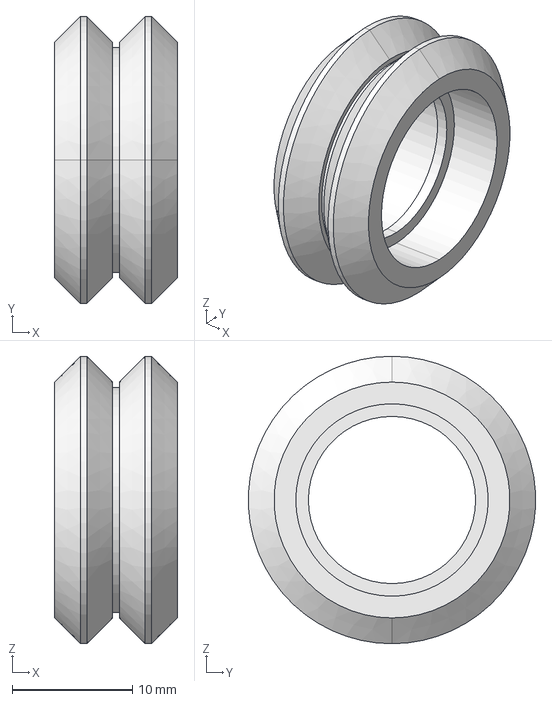
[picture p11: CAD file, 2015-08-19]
_hardware/OpenBuilds/2 - Wheels/Metal V Wheel.step.fcstd
10.2 x 23.9 x 23.9 mm

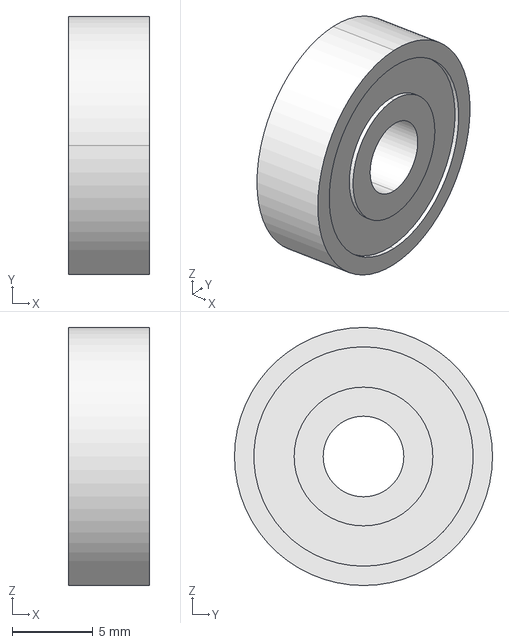
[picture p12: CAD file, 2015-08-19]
_hardware/OpenBuilds/3 - Bearings/Ball Bearing 5 x 16 x 5.step.fcstd
5.00 x 16.0 x 16.0 mm

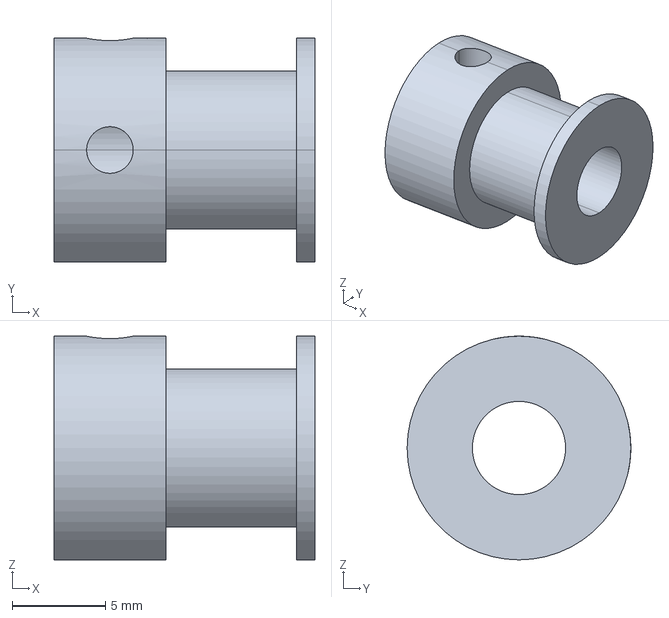
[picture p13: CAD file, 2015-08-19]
_hardware/OpenBuilds/4 - Pulleys/GT2 Timing Pulley 14 Tooth.step.fcstd
14.0 x 12.0 x 12.0 mm

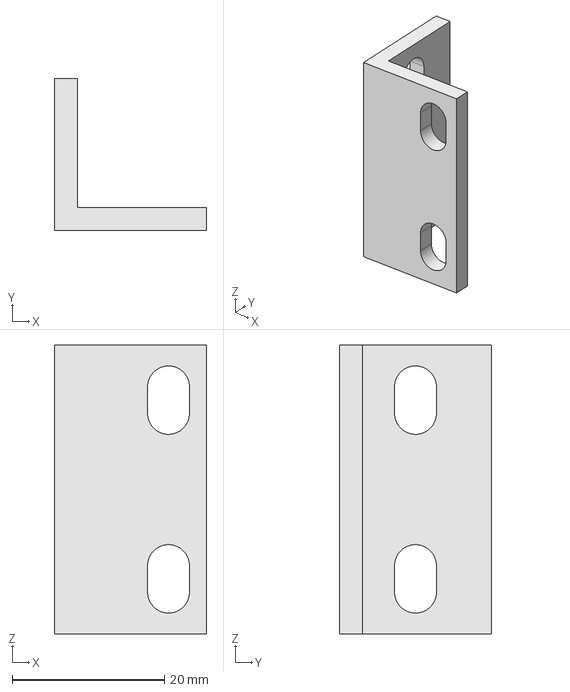
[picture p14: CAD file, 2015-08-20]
_hardware/OpenBuilds/5 - Brackets/L Bracket Double.step.fcstd
20.0 x 20.0 x 38.0 mm

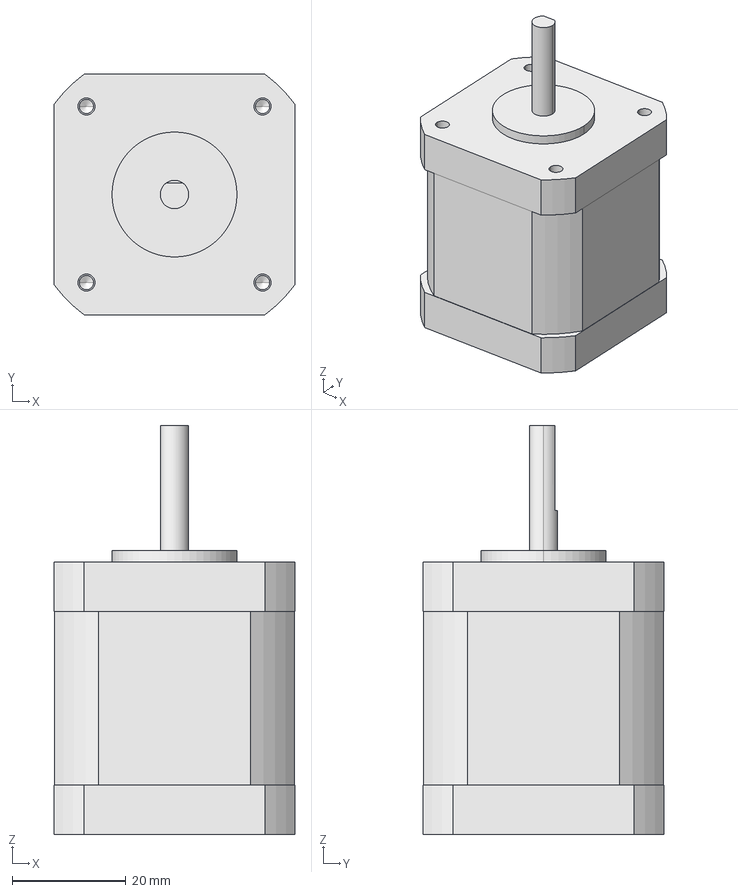
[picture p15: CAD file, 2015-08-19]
_hardware/OpenBuilds/6 - Electronics/Nema 17 Stepper Motor.step.fcstd
42.4 x 42.4 x 72.0 mm

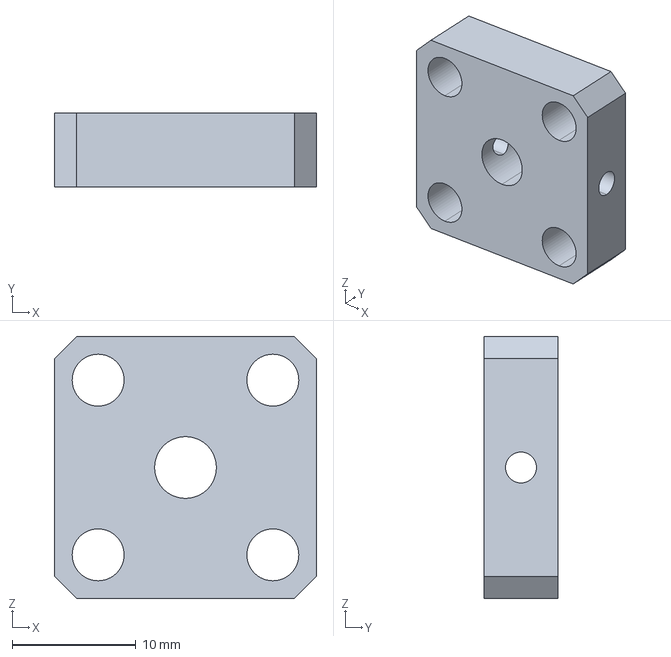
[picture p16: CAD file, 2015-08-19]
_hardware/OpenBuilds/7 - Hardware/Mounting Hub 5mm.step.fcstd
21.2 x 6.00 x 21.2 mm

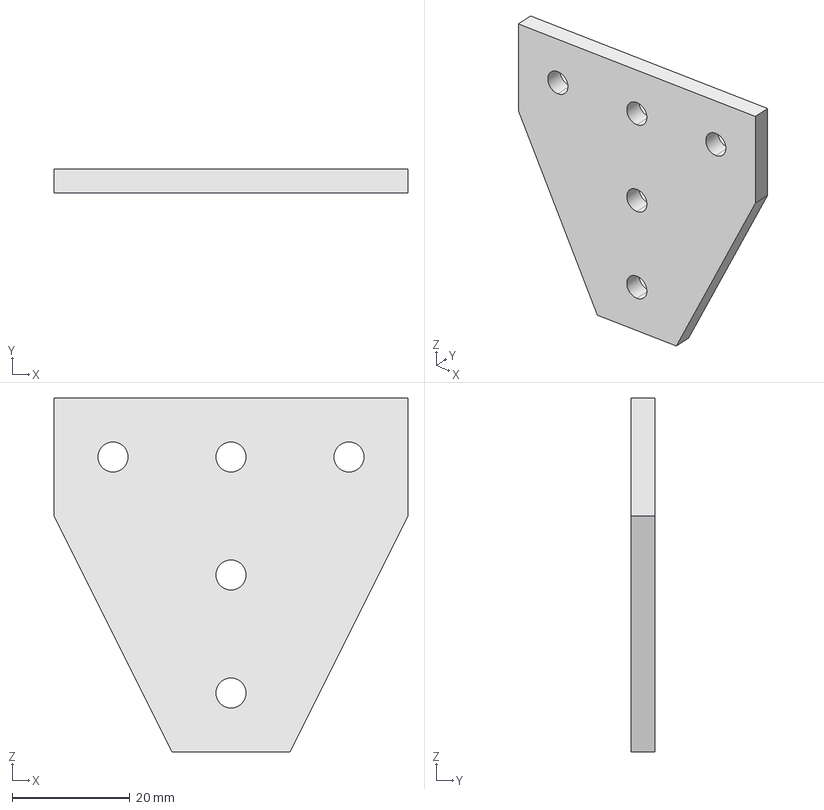
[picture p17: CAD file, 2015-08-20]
_hardware/OpenBuilds/8 - Plates/Joining Plate T.step.fcstd
60.0 x 4.00 x 60.0 mm

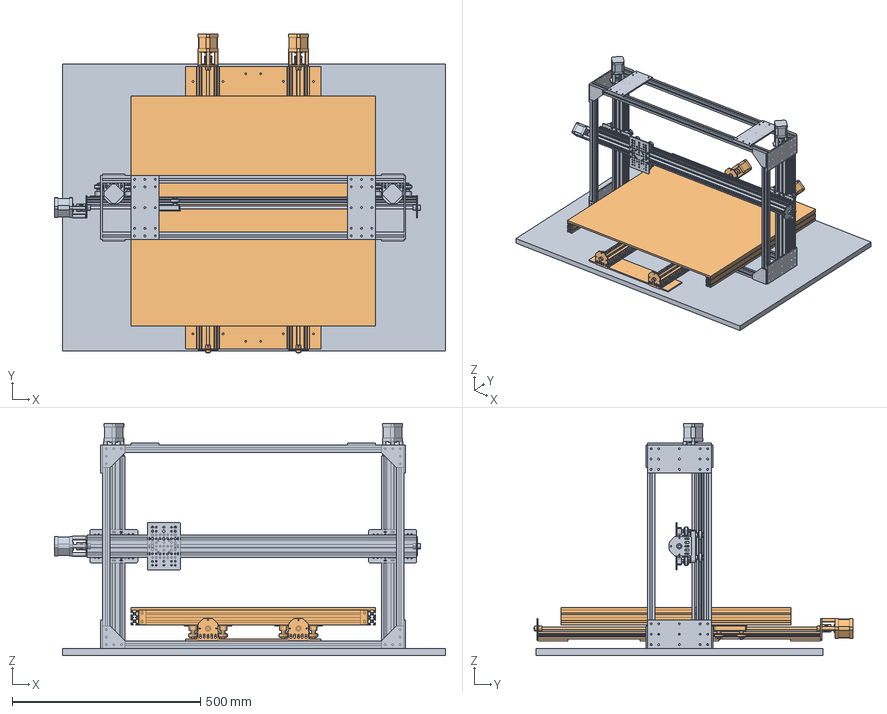
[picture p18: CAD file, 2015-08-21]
Axes/XYZ.fcstd
1037.9 x 847.0 x 616.0 mm
XZ_01
bed_01

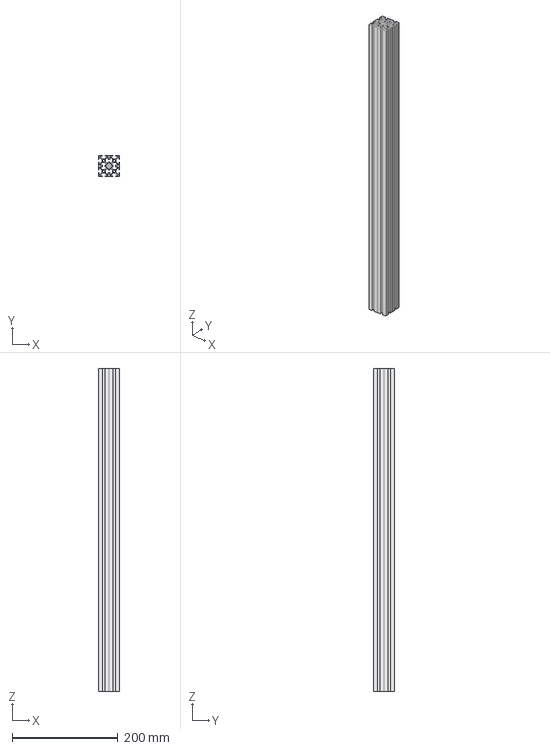
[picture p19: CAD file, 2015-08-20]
Bed/_support/20series-4x4-spar.fcstd
40.0 x 40.0 x 610.0 mm

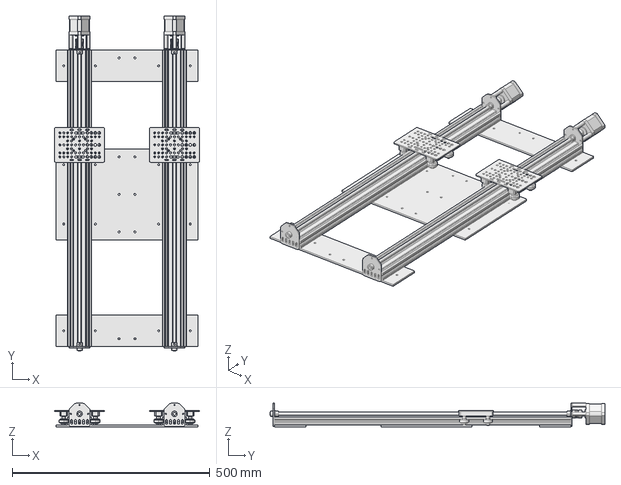
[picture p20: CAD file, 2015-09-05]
Bed/actuators.fcstd
367.0 x 847.0 x 59.8 mm

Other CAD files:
Bed/basic/JoiningPlates/XYplate.fcstd
Bed/basic/Layers/mdfBuildSurface.fcstd
Frame/basic/JoiningPlates/gantryPlate.fcstd
Frame/basic/Table/surface.fcstd
Axes/XZ.fcstd
Axes/Z.fcstd
Bed/_support/20series-1x2-rib.fcstd
Bed/basic/JoiningPlates/XYendplate.fcstd
Bed/bed.fcstd
Bed/carrier.fcstd
Bed/stackup.fcstd
Frame/gantry/_support/20series-1x1_X.fcstd
Frame/gantry/_support/20series-1x1_Z.fcstd
Frame/gantry/border.fcstd
Frame/gantry/structure.fcstd
_hardware/Extrusions/20series-1x2_610mm.fcstd
_hardware/Extrusions/_ref/20_series.DWG
_hardware/OpenBuilds/1 - Linear Rail/C-Beam 40x80x1000 Linear Rail.step.fcstd
_hardware/OpenBuilds/1 - Linear Rail/C-Beam 40x80x250 Linear Rail.step.fcstd
_hardware/OpenBuilds/1 - Linear Rail/C-Beam 40x80x500 Linear Rail.step.fcstd
_hardware/OpenBuilds/1 - Linear Rail/Open Rail 1000mm.step.fcstd
_hardware/OpenBuilds/1 - Linear Rail/Open Rail 1500mm.step.fcstd
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

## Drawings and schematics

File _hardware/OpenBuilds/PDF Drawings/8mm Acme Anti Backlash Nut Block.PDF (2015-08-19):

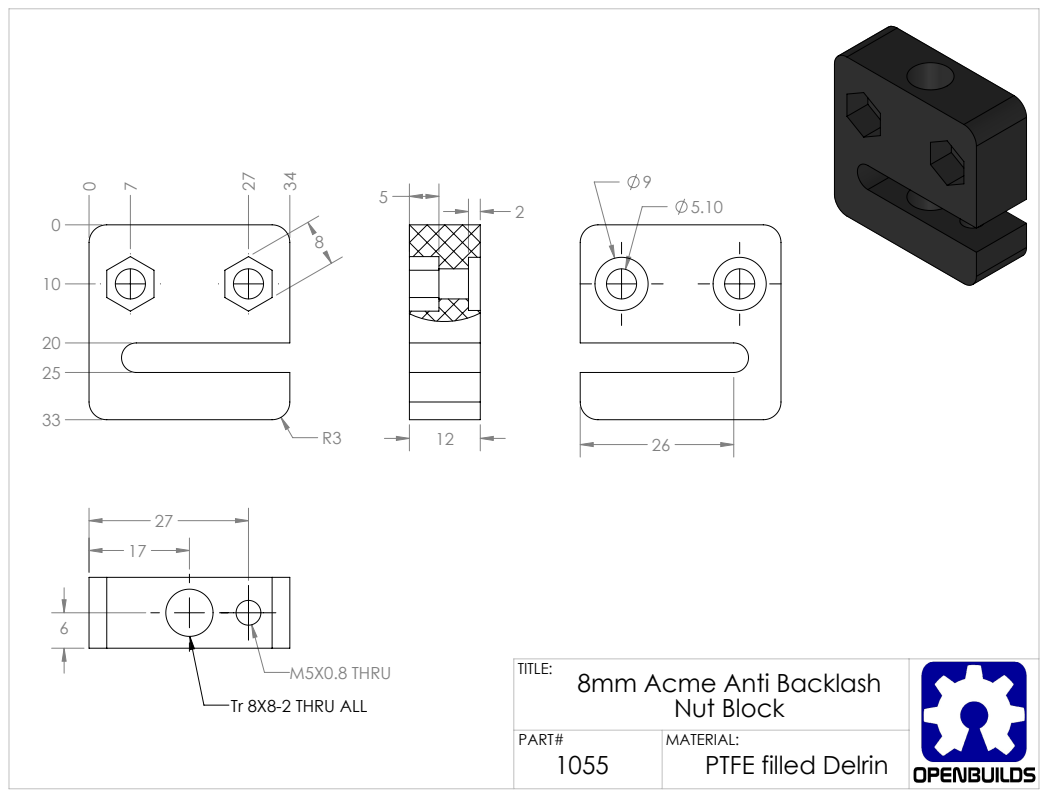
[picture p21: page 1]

M5X0.8 THRU
Tr 8X8-2 THRU ALL

TITLE: 8mm Acme Anti Backlash Nut Block

PART# 1055 | MATERIAL: PTFE filled Delrin

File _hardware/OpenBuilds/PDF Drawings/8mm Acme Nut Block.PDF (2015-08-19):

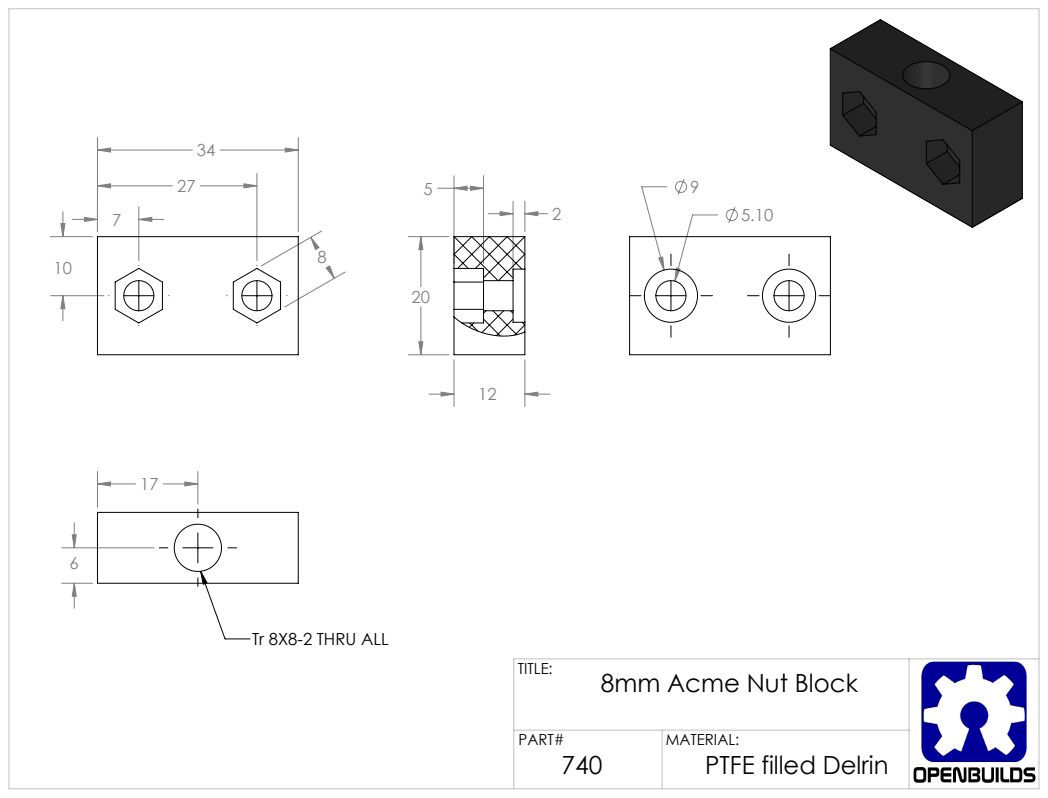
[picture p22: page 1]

Tr 8X8-2 THRU ALL

TITLE: 8mm Acme Nut Block

PART# 740 | MATERIAL: PTFE filled Delrin

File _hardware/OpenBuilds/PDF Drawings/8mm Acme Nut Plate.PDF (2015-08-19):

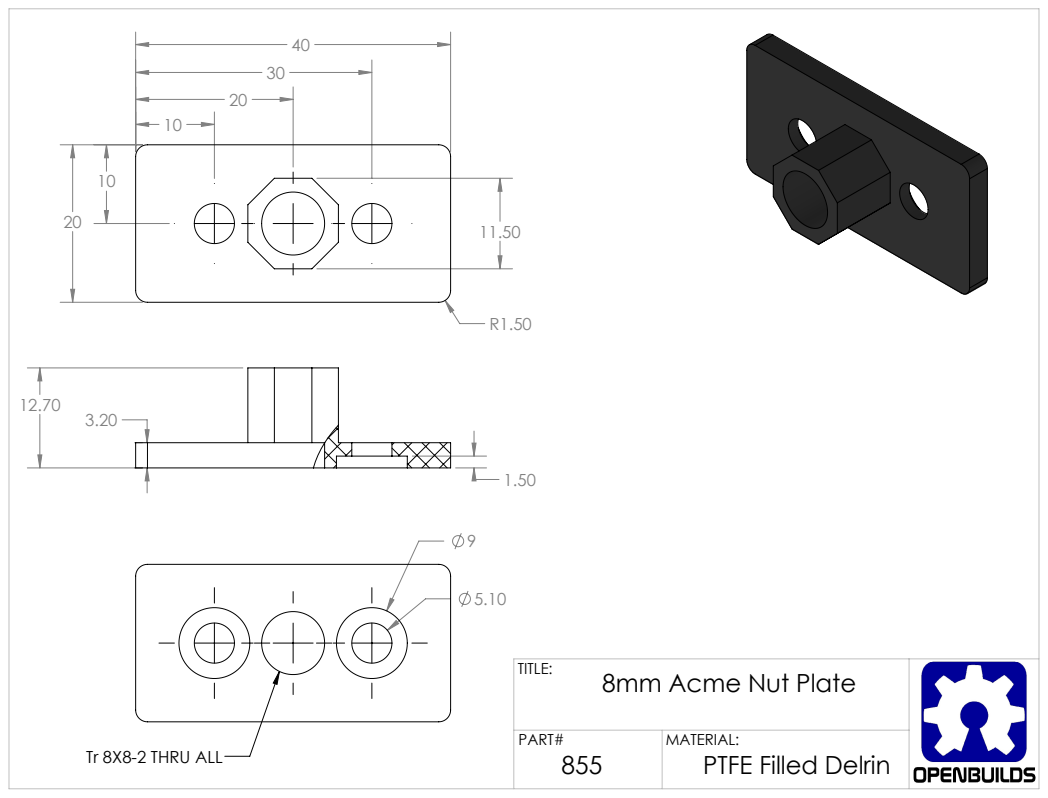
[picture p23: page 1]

TITLE: 8mm Acme Nut Plate

PART# 855 | MATERIAL: PTFE Filled Delrin

Tr 8X8-2 THRU ALL

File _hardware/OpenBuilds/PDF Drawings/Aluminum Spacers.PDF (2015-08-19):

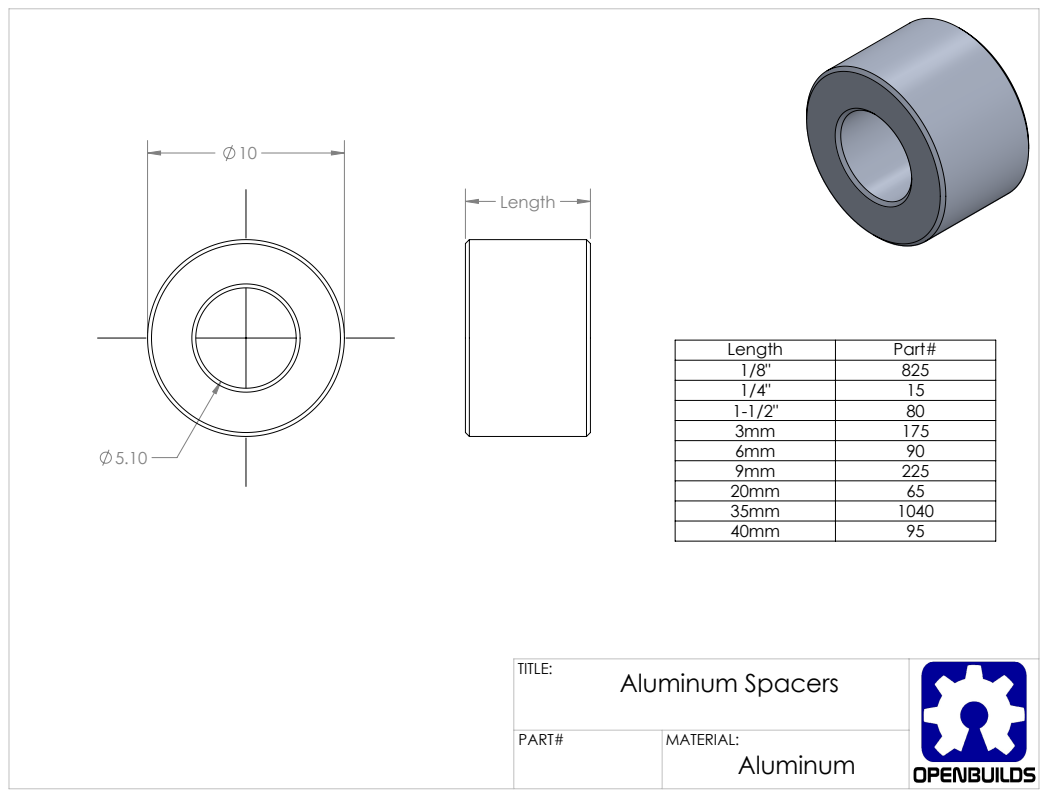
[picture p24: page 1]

Length | Part#
1/8" | 825
1/4" | 15
1-1/2" | 80
3mm | 175
6mm | 90
9mm | 225
20mm | 65
35mm | 1040
40mm | 95

TITLE: Aluminum Spacers

PART# | MATERIAL: Aluminum

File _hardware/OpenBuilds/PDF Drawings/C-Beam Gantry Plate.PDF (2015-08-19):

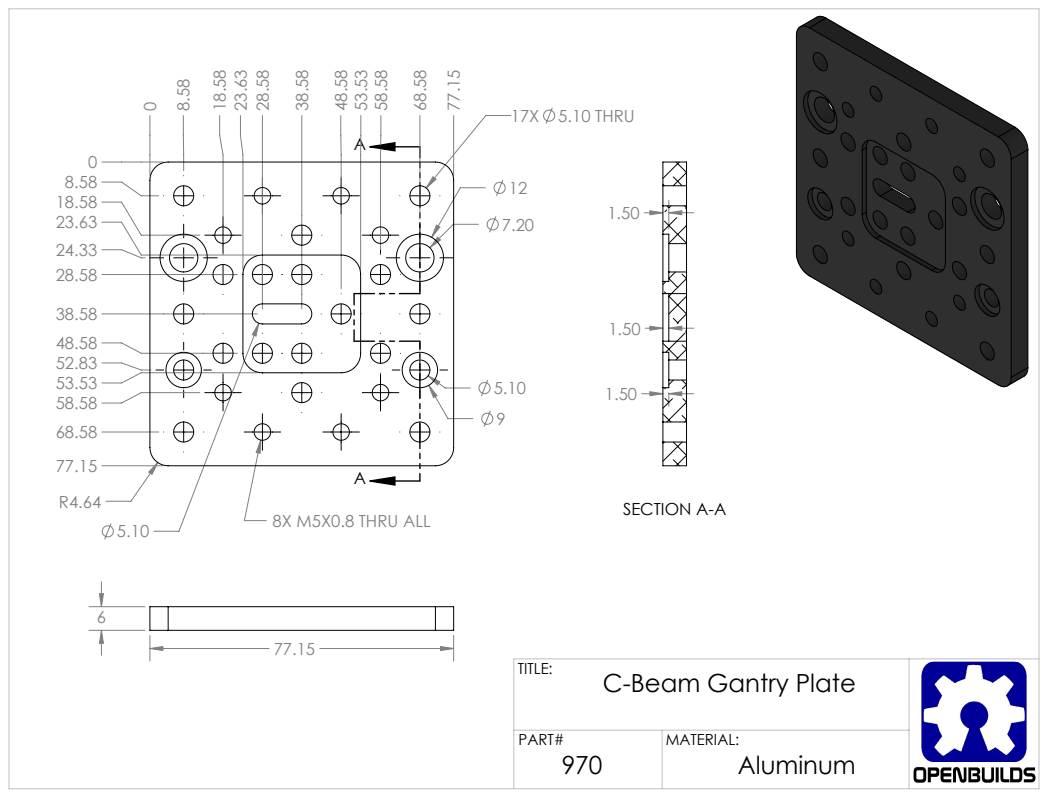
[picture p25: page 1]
8X M5X0.8 THRU ALL; 17X 5.10 THRU; SECTION A-A

TITLE: C-Beam Gantry Plate

PART# 970 | MATERIAL: Aluminum

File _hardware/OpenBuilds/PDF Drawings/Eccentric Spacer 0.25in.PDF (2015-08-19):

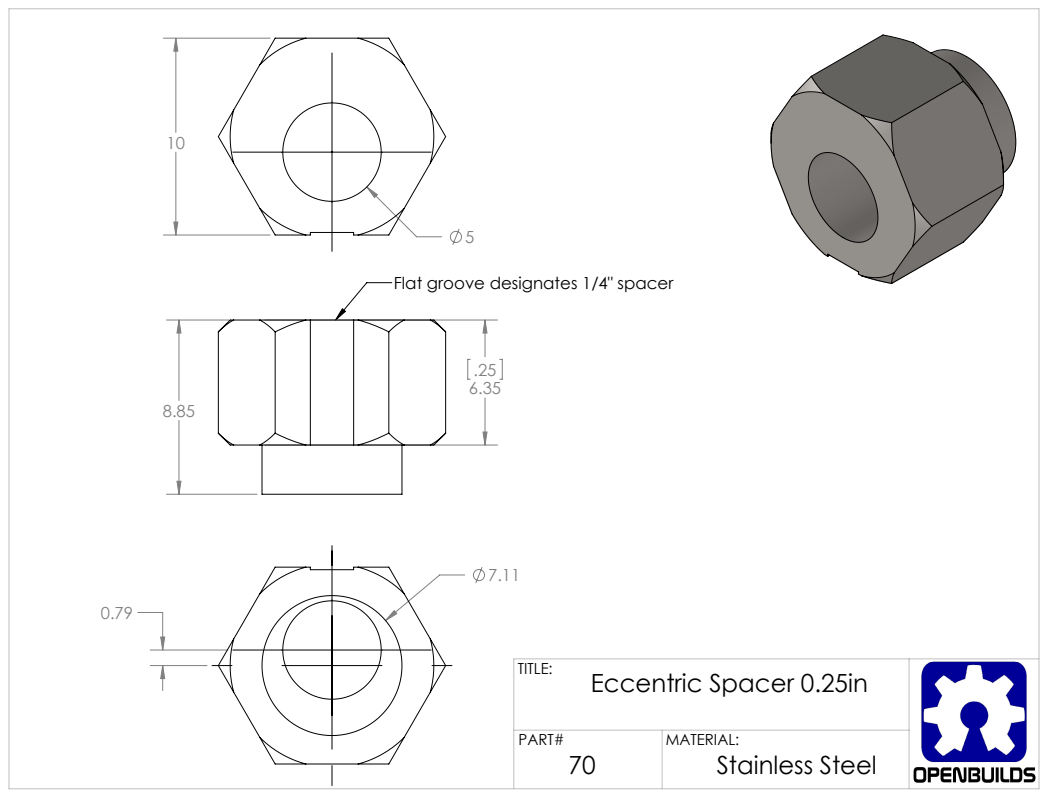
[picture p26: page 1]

Flat groove designates 1/4" spacer

TITLE: Eccentric Spacer 0.25in

PART# 70 | MATERIAL: Stainless Steel

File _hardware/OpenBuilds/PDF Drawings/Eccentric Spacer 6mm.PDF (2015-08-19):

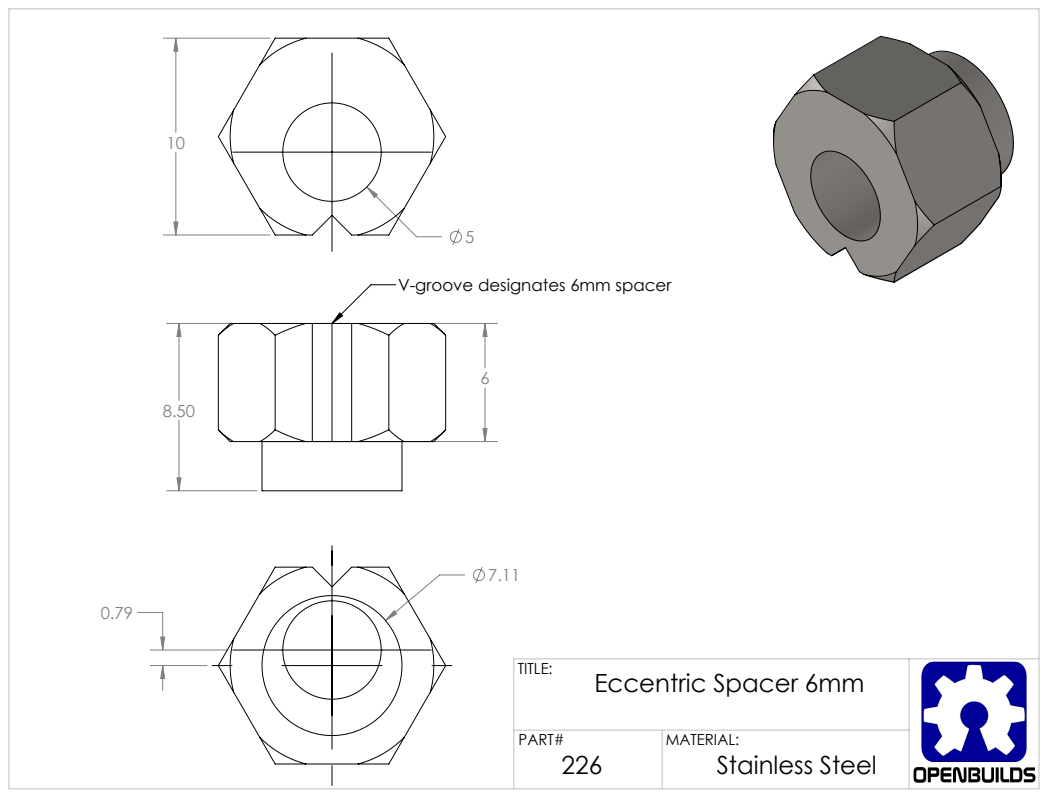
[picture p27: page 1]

V-groove designates 6mm spacer

TITLE: Eccentric Spacer 6mm

PART# 226 | MATERIAL: Stainless Steel

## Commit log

2015-08-17 Core assembly file moved.
    [Taz_Mega.SLDASM]
2015-08-19 Old CAD files purged.
    [20_series.SLDPRT, 20seriesCorner.SLDPRT, Gantry.SLDASM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]
2015-08-19 Frame rebuilt in FreeCAD.
    [20_series.DWG, 20_series.DXF, 20series-1x1_610mm.fcstd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]
2015-08-19 One Z-axis actuator mounted to frame.
    [gantry.fcstd, structure.fcstd]
2015-08-19 More realistic gantry plate positions.
    [gantry.fcstd, structure.fcstd]
2015-08-19 Additional mounting holes added to gantryPlate.
    [gantry.fcstd, gantryPlate.fcstd, structure.fcstd]
2015-08-19 Mounting brackets added for Z-Axis actuator.
    [Joining Strip Plate 2 Hole.step.fcstd, L Bracket Triple.step.fcstd, gantry.fcstd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]
2015-08-19 Frame X-axis widened to 800mm.
    [20series-1x1_X.fcstd, border.fcstd, gantry.fcstd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]
2015-08-19 Z-Axis lowered.
    [20series-1x1_Z.fcstd, border.fcstd, structure.fcstd]
2015-08-19 Z-Axis correctly positioned and bracketed.
    [gantry.fcstd, structure.fcstd]
2015-08-19 Both Z-axis actuators installed.
    [gantry.fcstd]
2015-08-19 Render update.
    [gantry.fcstd]
2015-08-19 New directory structure, Z and XZ axes in progress.
    [Z.fcstd]
2015-08-19 Experimental X-axis installed.
    [Z.fcstd]
2015-08-20 Usable XZ axes.
    [XZ.fcstd, Z.fcstd]
2015-08-20 XYplate sketch widget.
    [XYplate.fcstd]
2015-08-20 Complete CNC platform.
    [20_series.DWG, 20_series.DXF, 20series-1x1_610mm.fcstd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]
2015-08-21 Bill of Materials.
    [BOM.ods, XYZ.fcstd, XYendplate.fcstd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]
2015-08-22 BOM totaled, with eMachineShop estimates.
    [BOM.ods]
2015-08-25 Simplified BOM.
    [BOM.ods]
2015-08-26 Smaller scrap extrusions.
    [BOM.ods]
2015-09-05 XYplate dimensions corrected.
    [XYplate.fcstd, actuators.fcstd]
2015-09-05 Extra holes for compatibiltity with other Taz machines.
    [XYplate.fcstd]
